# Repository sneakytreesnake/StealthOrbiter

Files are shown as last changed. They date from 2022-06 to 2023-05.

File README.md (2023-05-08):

# StealthOrbiter
This mod aims to mount the Orbiter V2.0 extruder to the Voron Stealthburner & [crowncooler](https://github.com/sneakytreesnake/CrownCooler) assembly.



# Features
- It is fully compatible with the rest of the stealthburner system of hot ends & shrouds. A slightly modified version of the stealthburner fan shroud has been included to allow access to the orbiter filament lever.
- Compatible with the [Crown Cooler system.](https://github.com/sneakytreesnake/CrownCooler)
- Has a straight filament path. 
- Has an integrated filament sensor beneath the extruder for ERCF. Note that a filament sensor is not explicitly required anymore, but has been kept for legacy reasons.
- Works with cable chains or canbus boards
- Has a hinge feature integrated into the mount, to attach an aesthetic stealthburner shroud.

# Gallery

## Versions

| Standard Canbus  | PG7 Canbus | Cable Chain |
| --- | --- | --- |
|   |    |    |
| Standard Mount | PG7 Cable Gland Mount | Standard Mount |

There is a variation of the standard mount to incorporate a filament sensor below the extruder. See below.
## Stealthburner Build

  

## Crowncooler Build



## Filament sensor (for the filament sensor version):

There are a few inherent issues with the sensored mount so I do not recommend them. I highly recommend using the sensorless mounts instead, along with the Happy Hare ERCF software. 

If that answer doesn't satisfy you, there are a number of issues with the sensored mounts:
- requires supports
- sensor breaks the PTFE tube into two
- needs a pretty well calibrated printer to get the tolerance on the ball bearing hole right
- is actually LESS reliable than the sensorless version, as filament shavings from the extruder can work its way down into the ball bearing cavity, which jams it open
- eventually the filament rubbing on the hole around the ball bearing starts to wear through it and enlarge it



  

# Development Roadmap
1) [COMPLETE] Initial release!
2) [COMPELTE] Add ERCF filament sensor version
3) [COMPLETE] Add PG7 cable gland mount version
4) [COMPLETE] Assembly instructions

# Installation & BOM
 
 [Instructions are here.](https://github.com/sneakytreesnake/StealthOrbiter/tree/main/STL)

# Acknowledgments
- spacelab_2021, for providing the starting point I used in developing this mod
- KayosMaker, modified parts to make the canbus mounts

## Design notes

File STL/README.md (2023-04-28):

# Instructions

## Printing Orientation

The printing orientation is already set in the STL. Just import and print!

## Heatset Locations

### Standard Mount

 

BOM:
- 5x M3x4x5 heatset insert

Note: the heatset on the side is optional. It is used as a generic mount point.

### PG7 Straingland Mount

 

BOM:
- 4x M3x4x5 heatset insert

### Toolhead mount



BOM:
- 2x M3x4x5 heatset insert

## Extruder Subassembly

### Canbus Toolhead (EBB36, SHT36), Standard

 

 

BOM:
- 4x M3 washer
- 2x M3 nut
- 4x M3x12 SHCS
- 2x M3x15.3 Hex spacer
- EBB36/SHT36 toolhead 
- Orbiter V2.0
- ORBITERMOUNT_BASIC_V2.stl

### Canbus Toolhead (EBB36, SHT36), PG7 Straingland

 

 

BOM:
- 2x M3 washer
- 2x M3 nut
- 2x M3x12 SHCS
- 2x M3x20 Hex spacer
- 1x PG7 Strain gland 
- EBB36/SHT36 toolhead 
- Orbiter V2.0
- ORBITERMOUNT_PG7_V1.stl

### Cable Chain

 

 

BOM:
- 2x M3x8 SHCS
- 2x M3x40 BHCS
- 2x M3 nut
- Orbiter V2.0
- ORBITERMOUNT_BASIC_V2.stl
- [Orbiter_v2_Motor_Cover.stl](https://www.teamfdm.com/files/file/485-orbiter-2-clockwork-beta/)
- [Orbiter_v2_Generic_Chain_Anchor(Three_Hole)_v1.0.0 or Orbiter_v2_Chain_Anchor_Igus](https://www.teamfdm.com/files/file/485-orbiter-2-clockwork-beta/)

## Overally Toolhead Assembly

Mounts exactly the same as the Voron CW2 toolhead. Refer to the stealthburner assembly manual [here.](https://vorondesign.com/voron_stealthburner)

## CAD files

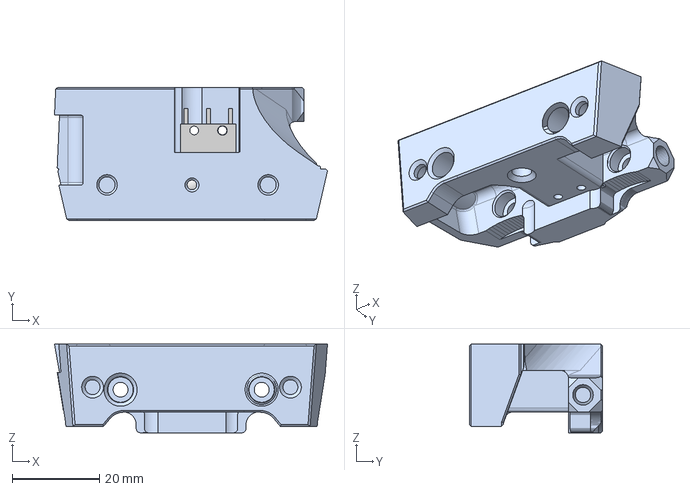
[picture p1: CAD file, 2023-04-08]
CAD/ORBITERMOUNT_SENSOR_V2.step
62.7 x 30.6 x 20.4 mm
Orbiter v2 Sensor v10 LDO FDM_1598K27_Hardened Bearing-Quality 440C S tainless Steel Ball

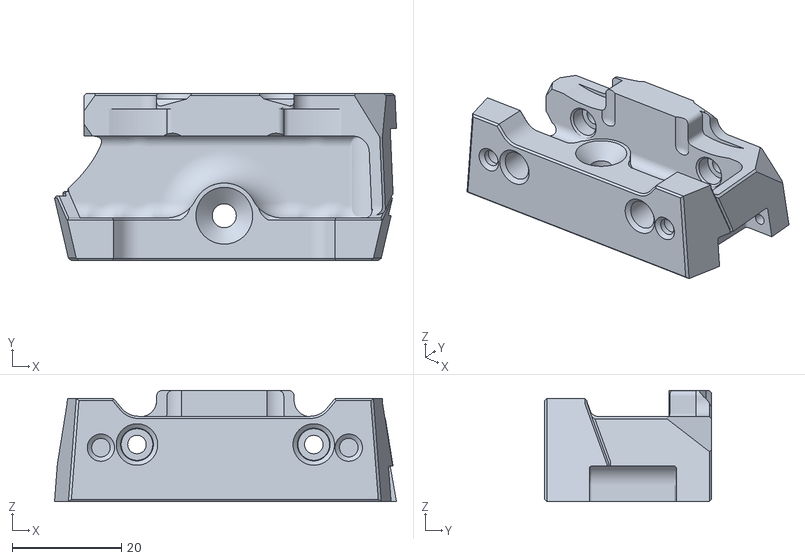
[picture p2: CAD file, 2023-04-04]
STL/ORBITERMOUNT_STANDARD_V3.stl
62.7 x 30.6 x 20.4

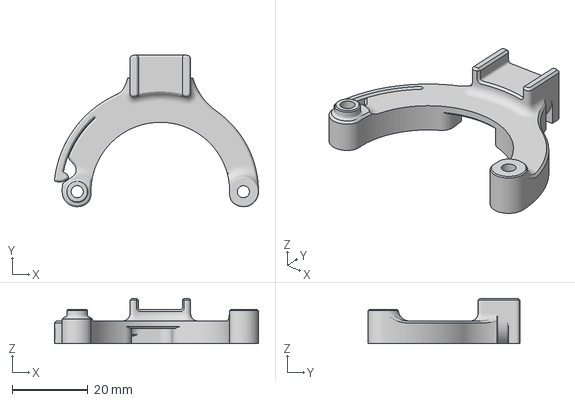
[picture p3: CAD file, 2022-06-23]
UMBILICAL_STRAINRELIEF_V5.3mf
53.8 x 40.0 x 12.0 mm

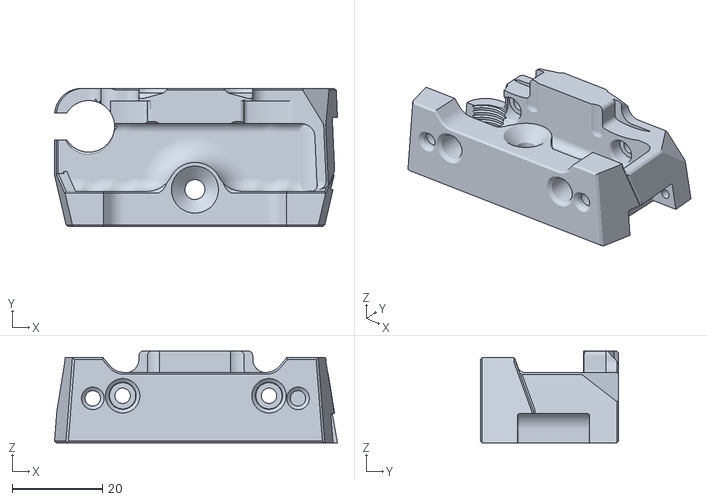
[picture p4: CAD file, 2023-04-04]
STL/ORBITERMOUNT_STANDARD_PG7_V2.stl
62.6 x 30.6 x 20.4

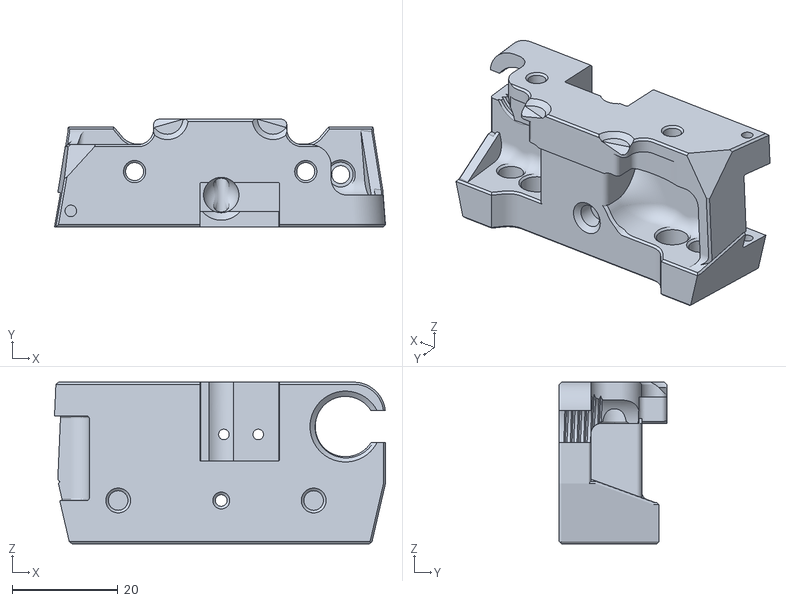
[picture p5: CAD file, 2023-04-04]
STL/ORBITERMOUNT_SENSOR_PG7_V1.stl
62.6 x 20.4 x 30.6

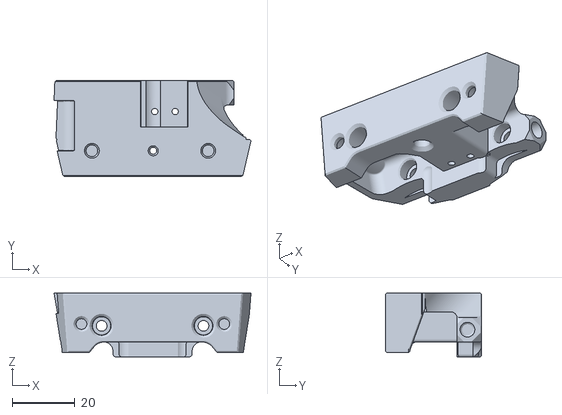
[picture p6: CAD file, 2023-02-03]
STL/ORBITERMOUNT_FILAMENTSENSOR_V1.stl
62.7 x 30.6 x 20.4

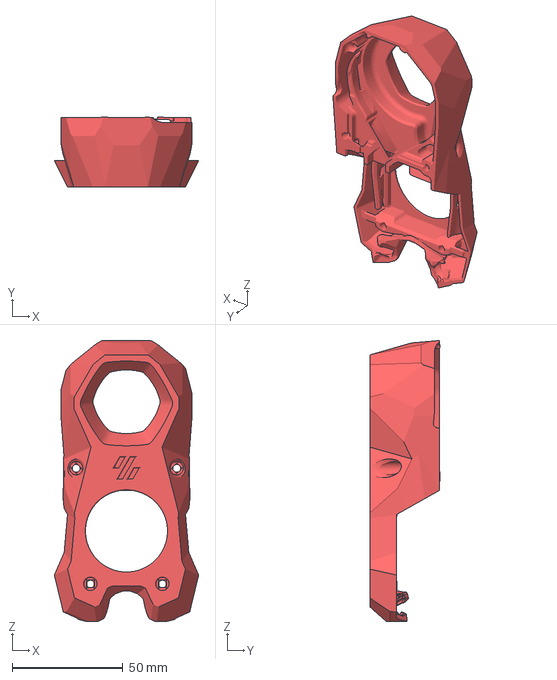
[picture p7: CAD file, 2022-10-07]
STL/stealthburner_body_levercut.3mf
65.1 x 31.8 x 126.8 mm

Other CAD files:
CAD/ORBITERv2_TOOLHEADMOUNT_V1.stl
STL/ORBITERMOUNT_BASIC_V2.stl
STL/ORBITERMOUNT_PG7_V1.stl
STL/ORBITER_TOOLHEADMOUNT v7.3mf
CAD/Obsolete/ORBITERTOOLHEAD.step
STL/Obsolete/ORBITERMOUNT_BASIC_V2.stl
STL/Obsolete/ORBITERMOUNT_PG7_V1.stl
STL/Obsolete/ORBITER_TOOLHEADMOUNT v7.3mf
STL/Obsolete/ORBITERv2_TOOLHEADMOUNT_V1.stl
STL/ORBITERMOUNT_SENSOR_V2.stl

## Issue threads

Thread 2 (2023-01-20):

filament_switch_sensor toolhead_sensor question

suizhenmin, 2023-01-20:
Hi orBiter Filament Sensor sensor releases V2.2 version. Now no matter how to set it, the filament state is displayed. How can I make it?

The following is my setting

[filament_switch_sensor toolhead_sensor]    
pause_on_runout: False
#runout_gcode: PAUSE #PAUSE WHEN FILAMENT RUNS OUT - DOES THIS SCREW WITH ERCF?
# filament sensor wired to the ERB or Printer MCU
#switch_pin: ercf:gpio25 #ERB
switch_pin: !PA1 #Printer MCU - FYSETC CHEETAH_MIX
#switch_pin: ^P1.27 #Printer MCU - BTT SKR board

sneakytreesnake, 2023-01-20:
It should just require inverting the pin in klipper config.

I believe the orbiter sensor page has more instructions on how to set the sensor software up.

suizhenmin, 2023-01-21:
Does the original OrbiterSensor.cfg configuration need to be disabled?

sneakytreesnake, 2023-01-21:
Yes disable the original .cfg file, and use the new OrbiterSensorV2.2.cfg file.

suizhenmin, 2023-01-22:
I almost gave up, now when the _ERCF_CALIBRATE is calibrated, the filament reaches the entrance of the extruder, but the extruder is in the state of returning material, maybe I will find an official Orbiter v2.0 base file to use ercf plan.

suizhenmin, 2023-01-22:
I checked your STL file, you used a material break detection alone, installed under the extruder base, can you provide the following BOM list?

sneakytreesnake, 2023-02-06:
I've added a BOM and updated the description to make the installation more clear.

Closed 2023-02-06.

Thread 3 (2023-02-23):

CAD Files

D1rect10ns, 2023-02-23:
Great work on this sneakytreesnake. Would you be willing to share the CAD files? I’d like to look at some modifications for my own setup?

sneakytreesnake, 2023-03-10:
Added a STEP file.

Closed 2023-03-20.

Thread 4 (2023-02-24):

Is there a mounting plate for ender3 v2 X carriage?

Gil80, 2023-02-24:
Hi!
This looks very good and I'd like to print the parts but I'm not too sure which parts and where to source them.
I use the Orbiter V2 with the Orbiter filament sensor and Phaetus Draghon HF hotend.
My ender 3 v2 X carriage is using wheels/rollers, not linear rails with 4010 heatbreak fan and 5015 radial fan.

Can you please help me to figure out which parts to print?

sneakytreesnake, 2023-02-26:
Hello, this mod uses the standard stealthburner carriage. I haven't done this myself, but if you manage to find an adapter plate (or design one) that adapts the stealthburner carriage to the ender 3 that would work.

A quick google search revealed this:

https://www.thingiverse.com/thing:5191205

and you should be able to print the rest from the Voron stealthburner Github repo

sneakytreesnake, 2023-02-26:
Closing as issue is not related to this mod.

Closed 2023-02-26.

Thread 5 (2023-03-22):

ORBITERMOUNT_BASIC includes the filament sensor

pringsen, 2023-03-22:
Wanted to go for the basic orbiter 2.0 mount without the filament sensor as i already have a runout sensor. However the version commited [6ee4ddf](https://github.com/sneakytreesnake/StealthOrbiter/commit/6ee4ddfd58f019e01a67f769358c1449047b22aa) includes the recess for the filament sensor.

https://github.com/sneakytreesnake/StealthOrbiter/blob/6ee4ddfd58f019e01a67f769358c1449047b22aa/STL/ORBITERMOUNT_BASIC_V1.stl

sneakytreesnake, 2023-03-22:
Not exactly sure how I mixed that up.... fixed now

Closed 2023-03-22.

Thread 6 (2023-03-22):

Print orientation question

DreamingRaven, 2023-03-22:
Hey quick question, the readme says "Print the mount with the front face on the bed (so the hold for the ball bearing is printed vertically). Use standard Voron print settings."

However I am unsure what the front face is on this model,
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

Is it this orientation? I assume I will need supports no matter which orientation I use.

Thanks, sorry for the relatively silly question, there are just two orientations it could be to keep the ball holder vertical if you don't know which side is the front.

sneakytreesnake, 2023-03-22:
Hello, I plan on updating the documentation soon to include printing instructions....

.. but until then, flip it 180 degree from how you have shown. So the face that is currently highest Z height is now on the bed. And correct, you will need supports for this model.

On this topic though, I would probably recommend using one of the other designs instead of the one with the filament sensor. If you are trying to use this with ERCF, the newer version of the software no longer needs a filament sensor below the extruder. I am running this software, and prefer sensorless to a dedicated filament sensor. [You can read about it more here.](https://github.com/moggieuk/ERCF-Software-V3)

Closed 2023-03-22.

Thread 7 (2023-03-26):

Install Guide

marc-gist, 2023-03-26:
Thank you for sharing! Do you have a link to any install guides/videos... I'm not really sure about how one installs on to the motor the chain guide, etc, or what exactly all the parts are that are needed to be printed between your stl and the linked one.

sneakytreesnake, 2023-03-26:
Give me a few days and I'll put together an install guide/video 😀

sneakytreesnake, 2023-04-01:
Hello, I've added a set of diagrams and descriptions. I've kept the links to the other design, as I don't yet have permission to upload them as part of this design.

Let me know how you get on, and if any other info would be useful!

sneakytreesnake, 2023-04-10:
Closed as install guide has been added, and no further comments made

Closed 2023-04-10.

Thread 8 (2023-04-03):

[REQ] Filament sensor version with PG7 gland

ndng28, 2023-04-03:
Hello, Thanks for working on this mod.

Is there a version of the mount with both the filament sensor and PG7 cable gland?

sneakytreesnake, 2023-04-04:
Hello,

No there isn't, but I'm happy to upload one. Expect it in the next day or so.

If you are trying to use the filament sensor with ERCF, I'd recommend using the sensorless branch. I am using it and find that it works flawlessly. You can read about it [here.](https://github.com/moggieuk/ERCF-Software-V3)

ndng28, 2023-04-04:
Thanks! I have read through discord and the post you linked at nauseam. From what I gathered was that it was more reliable to have a micro switch...I understand sensorless works really well but has to be setup "right" or else it wont work. I have already wasted time with a hall-sensor so was hoping to go the micro-switch route rather than sensorless.

Either way, I would super appreciate if you end up creating one with both (fila-sensor and PG7). Let me know if you have patreon or something I else where i can buy you a coffee :)

Cheers

sneakytreesnake, 2023-04-04:
I've added a PG7 filament sensor mount. Keep the print orientation the same (it's important the ball bearing runs smoothly in the hole). You will need to use supports.

Cheers for the offer but I am just glad other people find my work useful :-)

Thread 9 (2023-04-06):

[REQ] CAD files

bigbosshogg, 2023-04-06:
Thanks for your hard work on this project it is exactly what I needed! I noticed the only step file available is for the sensor version. Could you also put the standard and PG7 versions out there?

sneakytreesnake, 2023-04-10:
Uploaded all CAD variations now

Closed 2023-04-10.

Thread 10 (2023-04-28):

Orbiter touching the part cooling fan

Lwinz, 2023-04-28:
As title, orbiter touching the part cooling fan and press when tighten the front screw

sneakytreesnake, 2023-04-28:
Correct. This is “intended”.

I can’t move the orbiter without putting a bend/kink in the filament path, or breaking compatibility with the rest of the stealthburner parts.

As a result, the orbiter will touch the back of the fan. Since this doesn’t negatively affect anything, I considered this option better than linking the filament path.

Lwinz, 2023-04-28:
I will try reassembling it. Thanks for the reply

Closed 2023-05-08.

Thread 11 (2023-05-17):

Sensorless ERCF

appleimperio, 2023-05-17:
This is not an issue is more of a question. I'm planning to use the ERCF sensorless option and my orbiter 2 has the orbiter filament sensor. Can I use like that or I need a bowden coupler (as the manual suggest) instead of the light in the filament sensor?

sneakytreesnake, 2023-05-17:
I found the bowden tube was quite loose in the clear filament sensor part, and sometimes would pop out.

I ended up removing the orbiter sensor entirely as it was not needed and just caused issues for me.

Closed 2023-05-17.

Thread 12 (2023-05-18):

CAD for the cable mount?

thisiscam, 2023-05-18:
Hi,

Could you please release the step file for the cable mount? I have a mirrored orbiter and would like to tweak the cable mount to accomodate  that! Thank you!

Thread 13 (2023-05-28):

PG7 mount and ADXL345

garyd9, 2023-05-28:
Your suggested mounting for a Can bus toolhead using the PG7 mount has the CANBUS board mounted at an diagonal angle.  (here: https://github.com/sneakytreesnake/StealthOrbiter/tree/main/STL#canbus-toolhead-ebb36-sht36-pg7-straingland) This will likely result in the built ADXL345 becoming useless (because it can't differentiate which axis is which.)

It might be better to suggest using one of the MANY available CAN adapter mounts to ensure the adapter is mounted square with the toolhead.  For example: https://github.com/KayosMaker/CANboard_Mounts/blob/main/STLs/BTT_EBB36_1.0_Mounts/BTT_EBB36_1.0_mounts_plain/EBB36%201.0%20orbiter%202.0%20mount.stl

The adapter can even be mirrored so the adapter board is oriented with the CAN wiring going down (instead of up) to make wiring to the PG7 easier.

sneakytreesnake, 2023-05-28:
I don't believe that having the ADXL345 on a diagonal would cause any issues, input shaper takes the sum of the accelerations to determine the resonances. That's why you don't need to explicitly define or align the ADXL axis in klipper.

garyd9, 2023-05-29:
Perhaps you're right.  I'll have to give it a shot and see.  :)  Thank you for the model.  Trying to get things going with it now, but having a slight issue with the SB body.  I'll open another issue for that.

Closed 2023-05-29.

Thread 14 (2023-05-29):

Stealthburner body, lever cut - cut isn't long enough

garyd9, 2023-05-29:
I'm doing some test fittings with this model, and finding that the "cut" made to the SB body isn't long enough for the LDO Orbiter 2.0.  When the SB body is fully attached, the Orbiter lever won't close (at least not enough to make the filament even snug.)  (Or, if the orbiter lever is closed when assembling, the stealthburner part won't properly attach.)

I've attached two images.

The first (0919) is me trying to snip parts of the plastic off (and splitting layers) to try to get things to fit.

The second image (0920) is your original STL part attached with the orbiter filament lever closed. Note that cut out for the orbiter door isn't accommodating the lever.  Is it possible that LDO revised the lever part to make it larger and that's causing this problem?

(Note that I have filament inserted into the orbiter so the orbiter door isn't closed more than it might be in a real use situation.)

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

garyd9, 2023-05-29:
Here's another version of the SB body.  I took this from the latest SB github archive, and cut a larger space for the orbiter lever (and a bit of an internal piece to allow smooth movement.)  While I've test fitted this (and it has plenty of clearance), I haven't actually installed it in a working machine.

(These modifications are licensed under the original Voron license.  In other words, do with it what you'd like.)

[stealthburner_body_cut_for_orbiter.zip](https://github.com/sneakytreesnake/StealthOrbiter/files/11593727/stealthburner_body_cut_for_orbiter.zip)

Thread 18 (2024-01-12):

Canbus mount is missing

vananzz, 2024-01-12:
I can't find any stl or 3mf for this mount
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

cwestpha, 2024-01-16:
Honestly its likely better to use one of these: https://github.com/KayosMaker/CANboard_Mounts

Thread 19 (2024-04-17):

Idea: Incorporate filament cutter for ERCF.

justinr54321, 2024-04-17:
Can't find a way to contact, so, an idea. Make a filament cutter version for the ERCF. As one current issue is if you can't get the for tip tuned in, you get string built up in the extruder itself, causing a jam. WIth a filament cutter between the extruder and the hot end, it will eliminate the need to tune tip forming, allowing for a more user friendly version.

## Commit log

2022-07-31 Organising Files
    [ORBITERv2_TOOLHEADMOUNT_V1.stl, UMBILICAL_STRAINRELIEF_V5.3mf]
2022-07-31 ERCF Scripts
    Modified ERCF scripts to work with orbiter sensor placement.
    Works... barely...
    [ercf_hardware.cfg, ercf_software.cfg, ercf_vars.cfg]
2022-10-07 updated STLs
    [ORBITER_TOOLHEADMOUNT v7.3mf, ORBITERv2_TOOLHEADMOUNT_V1.stl, UMBILICAL_STRAINRELIEF_V5.3mf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]
2023-02-03 ERCF SUPPORT
    removed scripts, found to be unreliable. Added ERCF support via standard filament sensor below extruder
    [ORBITER_TOOLHEADMOUNT v7.3mf, OrbiterMountFilamentSensor_V1.stl, ercf_hardware.cfg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]
2023-03-10 added CAD file
    [ORBITERTOOLHEAD.step]
2023-03-17 added different mount options
    [ORBITERMOUNT_BASIC_V1.stl, ORBITERMOUNT_FILAMENTSENSOR_V1.stl, ORBITERMOUNT_PG7_V1.stl]
2023-03-22 updated basic mount to be correct version
    [ORBITERMOUNT_BASIC_V1.stl, ORBITERMOUNT_BASIC_V2.stl]
2023-04-04 moved to obsolete
    [ORBITERMOUNT_BASIC_V2.stl, ORBITERMOUNT_FILAMENTSENSOR_V1.stl, ORBITERMOUNT_PG7_V1.stl]
2023-04-04 created PG7 filament sensor mount
    [ORBITERMOUNT_SENSOR_PG7_V1.stl]
2023-04-04 fixed importing orientation
    [ORBITERMOUNT_SENSOR_V2.stl, ORBITERMOUNT_STANDARD_PG7_V2.stl, ORBITERMOUNT_STANDARD_V3.stl]
2023-04-08 moved obsolete CAD files
    [ORBITERTOOLHEAD.step]
2023-04-08 added CAD files of each design variation
    [ORBITERMOUNT_SENSOR_V2.step]
2023-04-28 updated printing instructions
2023-04-28 clarified the flaws of the sensorless mounts
    I intend to keep the sensorless versions to give people the choice.
